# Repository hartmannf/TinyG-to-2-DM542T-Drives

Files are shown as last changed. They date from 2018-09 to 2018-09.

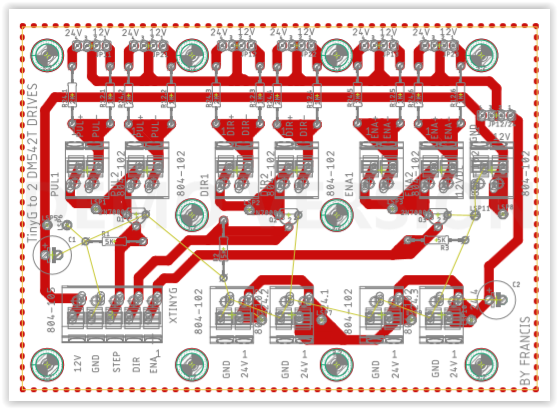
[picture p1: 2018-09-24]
DM542_PCB.PNG

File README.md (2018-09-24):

# TinyG-to-2-DM542T-Drives
TinyG to 2 DM542T Driver 12/24V Version

Original Idee was to connect on the TinyG v8 2 external stepperdriver of type DM542T to connect 2 Nema 23 on it. 
Thanks to Carl McGrath

Dokuments: 
Overview_TinyG_DM542T.pdf --> Typical application overview
DM542_PCB.PNG --> PCB view
DM542_PCB_top_Comp_.PNG --> Top View Components
DM542_SCH.PNG --> Schematic view
DM542T_Specification.pdf --> Driver Specification
Eagle_files
  --> DM542T.brd
  --> DM542T.SCH
  --> Eagle.epf
  
Function: 
Connect to tinyg v8 "Step, DIR,ENA" power with 12V from tinyg or 24V to where also the 2 DM542T Drivers are powered. with Jumpers switch Voltage can be be selected. 

Connection:
Connector: xTinyG to TinyG Board 
  12VDC -->  FAN 12VDC
  GND --> GND
  STEP --> STEP (Motor 1...4)
  DIR --> DIR (Motor 1...4)
  ENA --> ENABLE (Motor 1...4)

Connector: 24V1 .. 24V4
  GND --> Powersupply Ground
  24V1 --> Powersupply 24VDC

Connector for Drive 1 and 2:
  Pul+ --> Pul+
  Pul- --> Pul-
  DIR+ --> DIR+
  DIR- --> DIR-
  ENA+ --> ENA+
  ENA- --> ENA-
  
Voltage Selector
  JP12/24 selects the Power Source 12V if powered by TinyG or 24V if Powered with same Powersource like DM542T 
  JP12.1 .. JP12.6 if 12V Powerd from TinyG
  JP24.1 .. JP24.6 if Powered same then DM542T 
  BE AWARE OF: Power Source can only be either 12V or 24V.

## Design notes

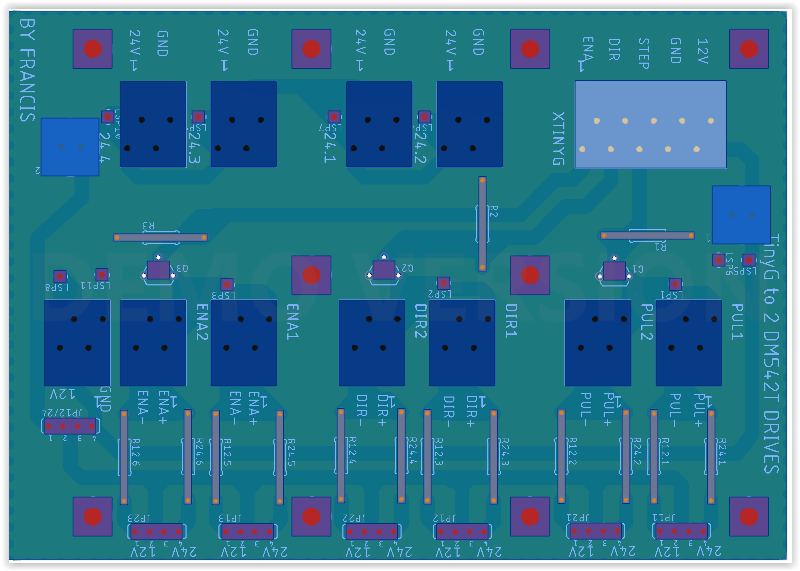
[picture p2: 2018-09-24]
DM542_PCB_top_Comp_.PNG

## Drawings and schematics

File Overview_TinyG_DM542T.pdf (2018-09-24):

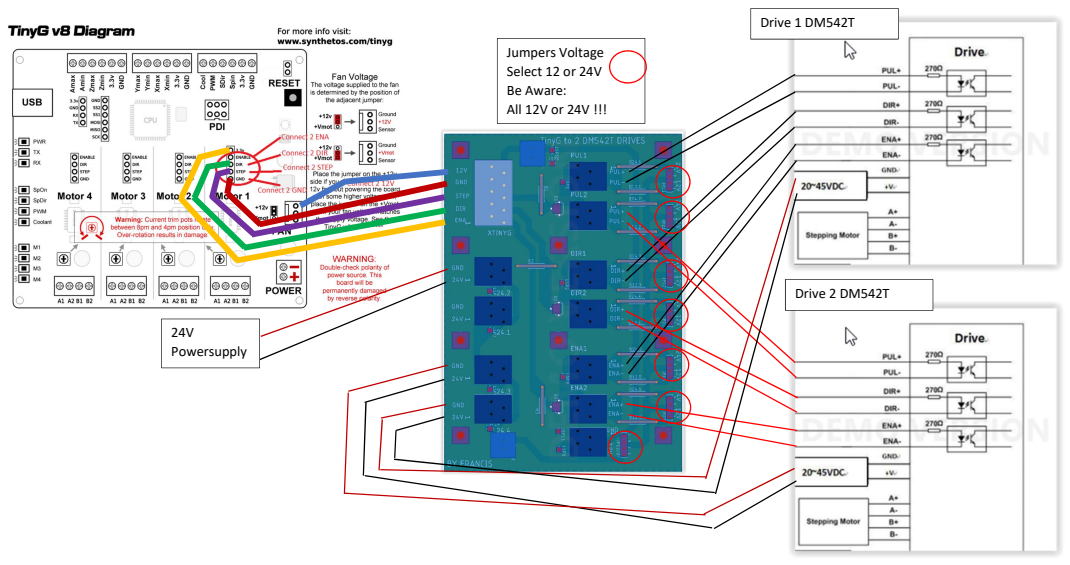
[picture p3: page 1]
Jumpers Voltage Select 12 or 24V Be Aware: All 12V or 24V !!!; 24V Powersupply; Drive 1 DM542T; Drive 2 DM542T

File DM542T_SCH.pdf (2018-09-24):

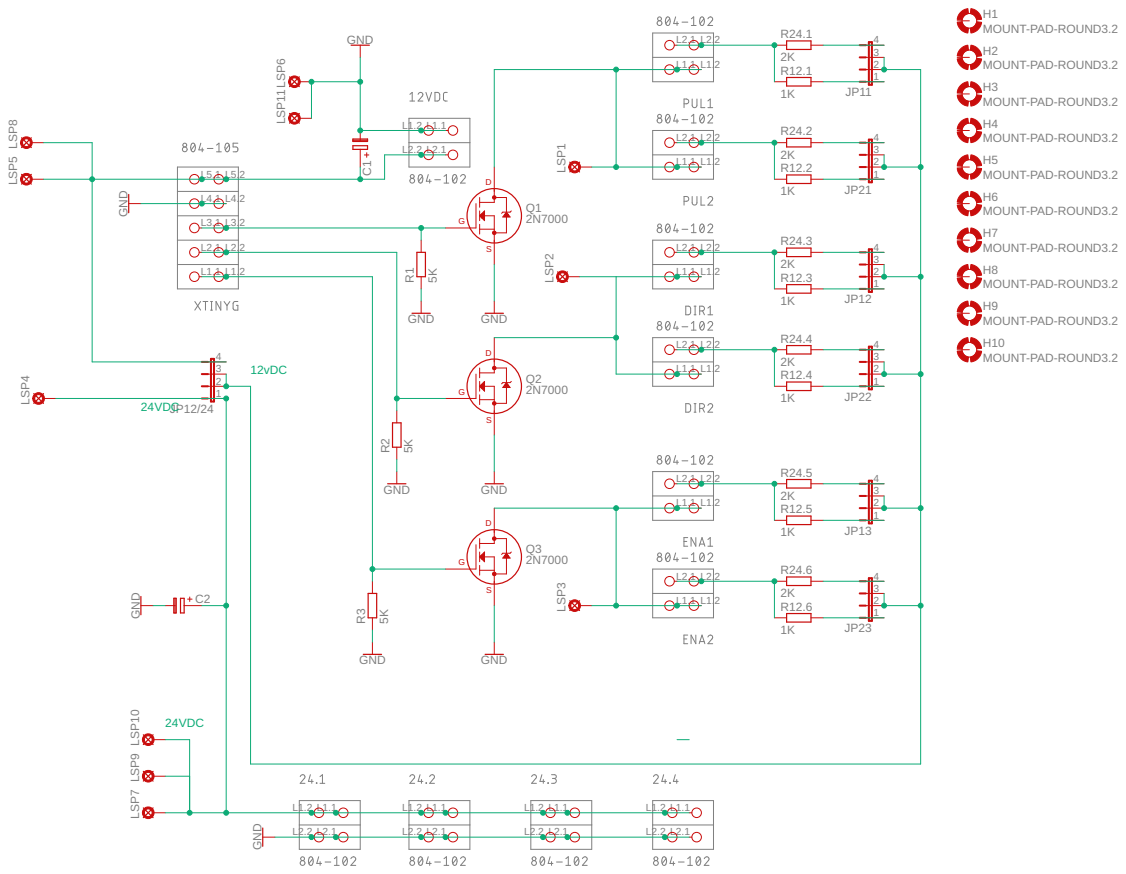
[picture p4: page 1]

GND GND 2K1K2K1K2K1K GND GND GND 5K 5K 5K GNDGNDGND 2K1K2K1K2K1K GND GND MOUNT-PAD-ROUND3.2 MOUNT-PAD-ROUND3.2 MOUNT-PAD-ROUND3.2 MOUNT-PAD-ROUND3.2 MOUNT-PAD-ROUND3.2 MOUNT-PAD-ROUND3.2 MOUNT-PAD-ROUND3.2 MOUNT-PAD-ROUND3.2 MOUNT-PAD-ROUND3.2 MOUNT-PAD-ROUND3.2 2N7000 2N7000 2N7000 L1.1 L2.1 L1.2 L2.2 L1.1 L2.1 L1.2 L2.2 L1.1 L2.1 L1.2 L2.2 L1.2 L2.2 L3.2 L1.1 L2.1 L3.1 L4.1 L5.1 L4.2 L5.2 L1.1 L2.1 L1.2 L2.2 L1.1 L2.1 L1.2 L2.2 L1.1 L2.1 L1.2 L2.2 JP11 1234 R24.1 R12.1 R24.3 R12.3 JP12 1234 R24.5 R12.5 JP13 1234 JP12/24 1234 R1 R2 R3 L1.1 L2.1 L1.2 L2.2 L1.1 L2.1 L1.2 L2.2 L1.1 L2.1 L1.2 L2.2 R24.2 R12.2 JP21 1234 R24.4 R12.4 JP22 1234 JP23 1234 R24.6 R12.6 L1.1 L2.1 L1.2 L2.2 C1 C2 L1.1 L2.1 L1.2 L2.2 LSP1 LSP2 LSP3 LSP4 LSP5 LSP6 LSP7 LSP8 LSP9 LSP10 LSP11 H1 H2 H3 H4 H5 H6 H7 H8 H9 H10 Q1 Q2 Q3 D G SD G SD G S 12vDC 24VDC24VDC

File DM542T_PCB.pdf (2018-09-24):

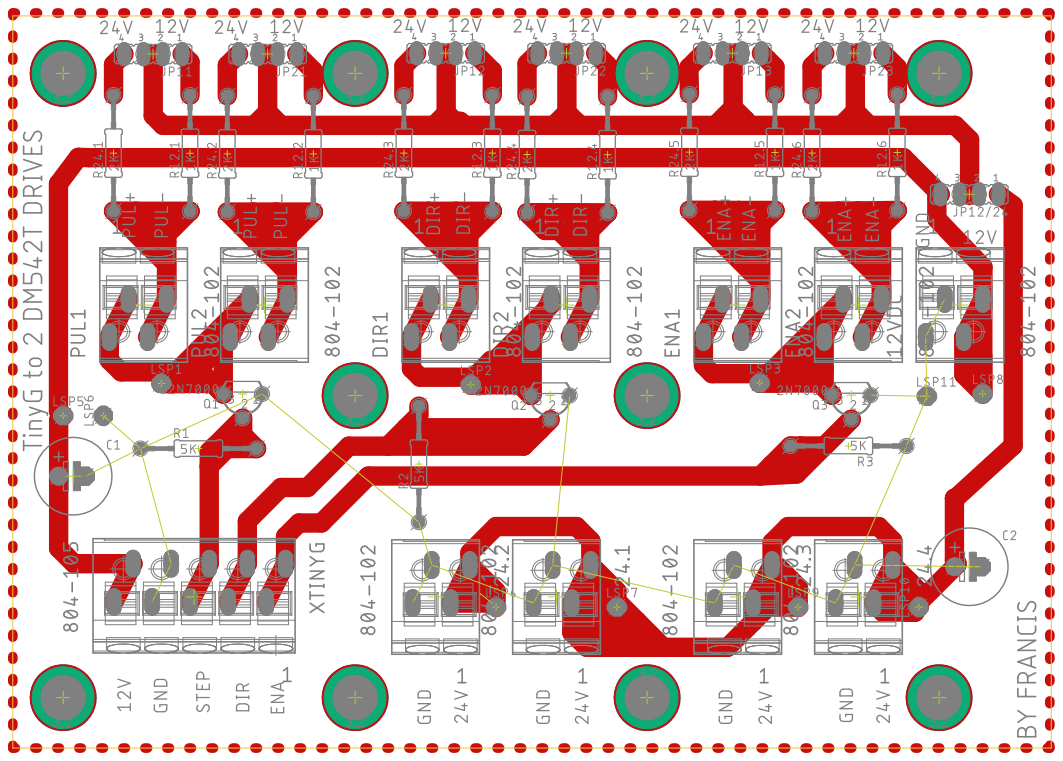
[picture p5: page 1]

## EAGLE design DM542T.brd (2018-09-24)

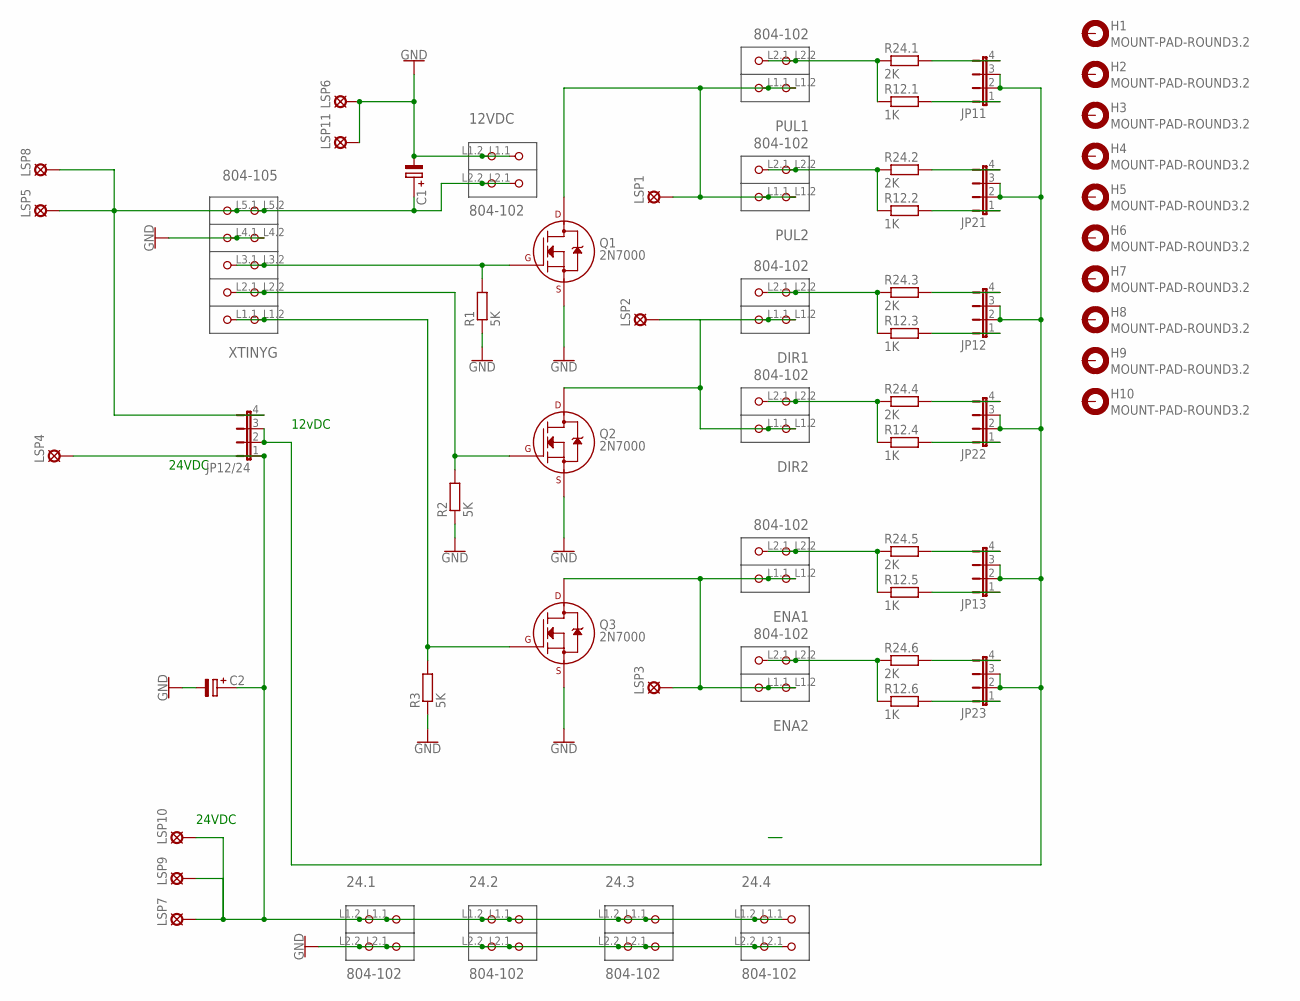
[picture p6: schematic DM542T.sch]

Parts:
12VDC, 24.1, 24.2, 24.3, 24.4: 804-102; P-804-102
C1, C2: C-PR-3,5X10; E3,5-10
DIR1, DIR2: 804-102; P-804-102
ENA1, ENA2: 804-102; P-804-102
H1, H2, H3, H4, H5, H6, H7, H8, H9, H10: MOUNT-PAD-ROUND3.2; 3,2-PAD
JP11, JP12, JP12/24, JP13, JP21, JP22, JP23: JP4E; JP4
LSP1, LSP2, LSP3, LSP4, LSP5, LSP6, LSP7, LSP8, LSP9, LSP10, LSP11: LSP10
PUL1, PUL2: 804-102; P-804-102
Q1, Q2, Q3: 2N7000; TO-92
R1, R2, R3: 5K; 0207/15
R12.1, R12.2, R12.3, R12.4, R12.5, R12.6: 1K; 0207/15
R24.1, R24.2, R24.3, R24.4, R24.5, R24.6: 2K; 0207/15
XTINYG: 804-105; P-804-105

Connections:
GND: 12VDC.L1.1 (P1.1), 12VDC.L1.2 (P1.2), 24.1.L2.1 (P2.1), 24.1.L2.2 (P2.2), 24.2.L2.1 (P2.1), 24.2.L2.2 (P2.2), 24.3.L2.1 (P2.1), 24.3.L2.2 (P2.2), 24.4.L2.1 (P2.1), 24.4.L2.2 (P2.2), C1.-, C2.-, LSP6.MP, LSP11.MP, Q1.1 (S), Q2.1 (S), Q3.1 (S), R1.1, R2.1, R3.1, XTINYG.L4.1 (P4.1), XTINYG.L4.2 (P4.2)
unnamed: PUL1.L2.1 (P2.1), PUL1.L2.2 (P2.2), R12.1.1, R24.1.1
unnamed: 12VDC.L2.1 (P2.1), 12VDC.L2.2 (P2.2), C1.+, JP12/24.4, LSP5.MP, LSP8.MP, XTINYG.L5.1 (P5.1), XTINYG.L5.2 (P5.2)
unnamed: Q2.2 (G), R2.2, XTINYG.L2.1 (P2.1), XTINYG.L2.2 (P2.2)
unnamed: Q3.2 (G), R3.2, XTINYG.L1.1 (P1.1), XTINYG.L1.2 (P1.2)
unnamed: DIR1.L1.1 (P1.1), DIR1.L1.2 (P1.2), DIR2.L1.1 (P1.1), DIR2.L1.2 (P1.2), LSP2.MP, Q2.3 (D)
unnamed: 24.1.L1.1 (P1.1), 24.1.L1.2 (P1.2), 24.2.L1.1 (P1.1), 24.2.L1.2 (P1.2), 24.3.L1.1 (P1.1), 24.3.L1.2 (P1.2), 24.4.L1.1 (P1.1), 24.4.L1.2 (P1.2), C2.+, JP12/24.1, LSP4.MP, LSP7.MP, LSP9.MP, LSP10.MP
unnamed: JP11.4, R24.1.2
unnamed: LSP1.MP, PUL1.L1.1 (P1.1), PUL1.L1.2 (P1.2), PUL2.L1.1 (P1.1), PUL2.L1.2 (P1.2), Q1.3 (D)
unnamed: PUL2.L2.1 (P2.1), PUL2.L2.2 (P2.2), R12.2.1, R24.2.1
unnamed: JP11.1, R12.1.2
unnamed: JP13.4, R24.5.2
unnamed: JP12.1, R12.3.2
unnamed: JP22.4, R24.4.2
unnamed: JP13.1, R12.5.2
unnamed: DIR1.L2.1 (P2.1), DIR1.L2.2 (P2.2), R12.3.1, R24.3.1
unnamed: JP11.2, JP11.3, JP12.2, JP12.3, JP12/24.2, JP12/24.3, JP13.2, JP13.3, JP21.2, JP21.3, JP22.2, JP22.3, JP23.2, JP23.3
unnamed: JP12.4, R24.3.2
unnamed: ENA1.L2.1 (P2.1), ENA1.L2.2 (P2.2), R12.5.1, R24.5.1
unnamed: JP21.1, R12.2.2
unnamed: JP23.4, R24.6.2
unnamed: JP23.1, R12.6.2
unnamed: ENA2.L2.1 (P2.1), ENA2.L2.2 (P2.2), R12.6.1, R24.6.1
unnamed: JP21.4, R24.2.2
unnamed: ENA1.L1.1 (P1.1), ENA1.L1.2 (P1.2), ENA2.L1.1 (P1.1), ENA2.L1.2 (P1.2), LSP3.MP, Q3.3 (D)
unnamed: DIR2.L2.1 (P2.1), DIR2.L2.2 (P2.2), R12.4.1, R24.4.1
unnamed: JP22.1, R12.4.2
unnamed: Q1.2 (G), R1.2, XTINYG.L3.1 (P3.1), XTINYG.L3.2 (P3.2)

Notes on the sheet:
12vDC
24VDC

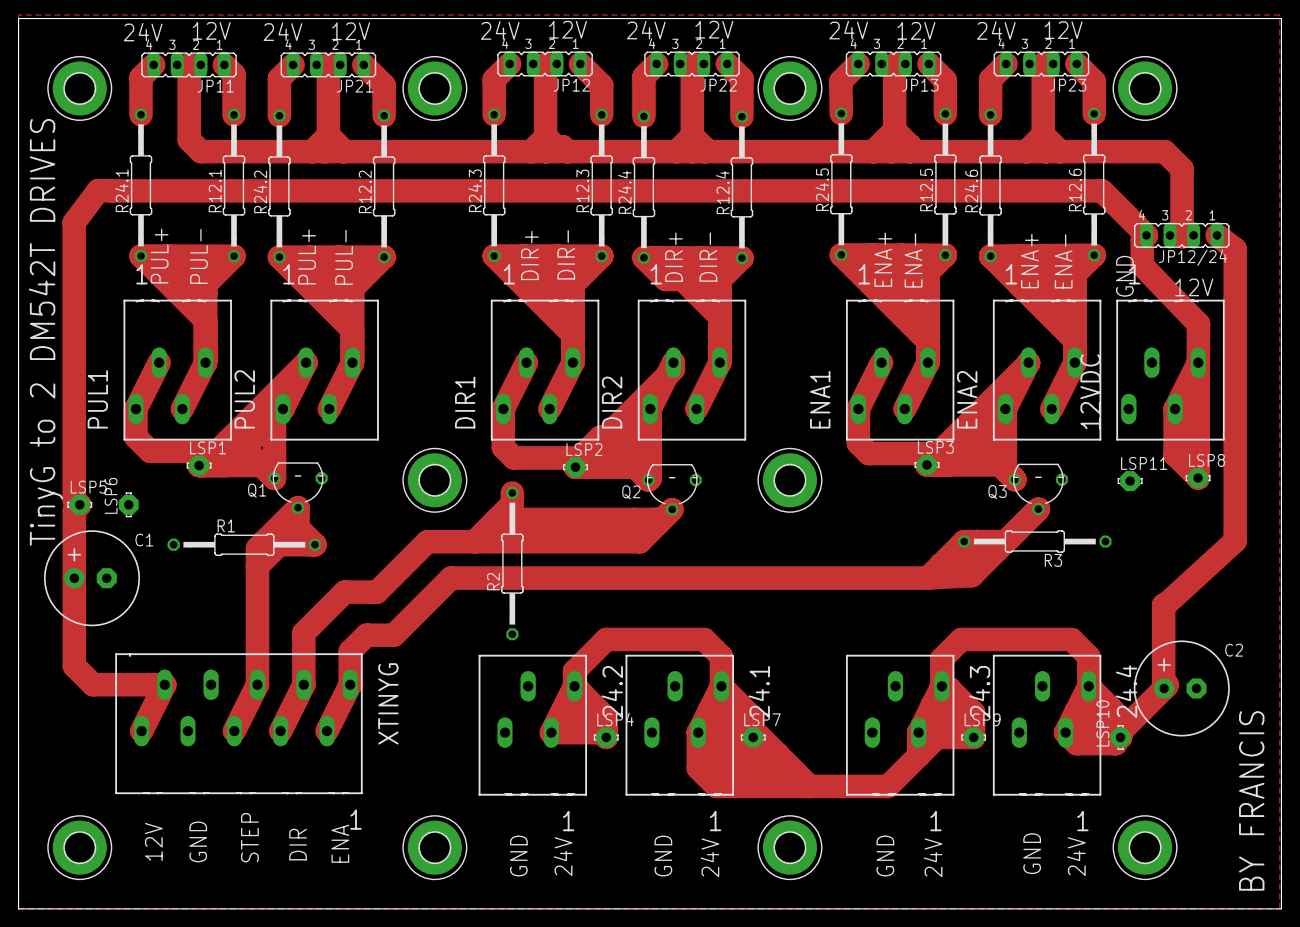
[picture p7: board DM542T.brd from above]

Board: 2 copper layers, 136.2 x 96.0 mm, 60 parts (0 on the bottom side), 28 nets.

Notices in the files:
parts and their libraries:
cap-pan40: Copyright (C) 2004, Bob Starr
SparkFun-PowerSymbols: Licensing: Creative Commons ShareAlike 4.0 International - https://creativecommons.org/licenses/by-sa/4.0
